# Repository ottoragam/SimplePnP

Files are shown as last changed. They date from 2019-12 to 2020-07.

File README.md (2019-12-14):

# SimplePnP
Your personal open-hardware PCB assembly machine

----------------------------------------------------------------------
SimplePnP (c) by Gino Magarotto

SimplePnP is licensed under a
Creative Commons Attribution-ShareAlike 3.0 Unported License.

You should have received a copy of the license along with this
work.  If not, see <http://creativecommons.org/licenses/by-sa/3.0/>.

----------------------------------------------------------------------
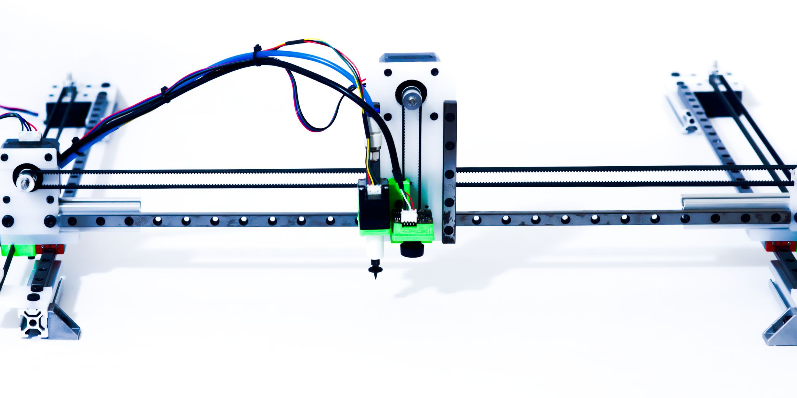
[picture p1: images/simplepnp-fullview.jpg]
drive


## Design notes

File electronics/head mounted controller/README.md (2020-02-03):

Small form factor ATmega328p based GRBL booard. Connects to TMC2209 stepper driver board.

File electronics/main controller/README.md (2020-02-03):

Small form factor ATmega328p based GRBL booard. Connects to TMC2209 stepper driver board. For controlling the pick and place table motors. Needs two USB-UART converter cables like ones based around CH340 and CP2102 chips.

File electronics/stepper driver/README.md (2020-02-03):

Carrier board for three TMC2209 stepper drivers. Standard and serial pins broken out. Fixed current limit.

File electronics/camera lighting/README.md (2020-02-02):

LED carrier board for pick and place camera illumination. 5V PWM input.

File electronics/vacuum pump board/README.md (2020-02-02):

Mosfet switch board for 12VDC vacuum pump. Solder the motor terminals directly to the PCB.

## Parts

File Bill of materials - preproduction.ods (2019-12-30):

Bill of materials for SimplePnP
Part | Qty | Notes
bridge-carriageplate | 2 | custom design for SimplePnP
gt2-idlerbracket | 3 | custom design for SimplePnP
nema17-bracket | 3 | custom design for SimplePnP
vacuum-head | 1 | custom design for SimplePnP
100mm 2020 extrusion | 6 | generic
M5x8 bolt | 20 | socket head or button head
M5 T-slot nut | 20 | generic
M3x6 bolt | 55 | socket head
M3x6 flat head bolt | 20 | socket head
M3x12 bolt | 14 | socket head
M3 T-slot nut | 12 | generic
M3 9mm brass standoff | 6 | 10mm works but may need a flat washer to remove pulley play
axisbelt-clamp | 3 | custom design for SimplePnP
headbelt-clamp | 2 | custom design for SimplePnP
headcamera-bracket | 1 | custom design for SimplePnP
nema8-bracket | 2 | custom design for SimplePnP
Bottomcamera-mount | 1 | custom design for SimplePnP
nema8 motor 8HY0001-7SK | 2
nema17 motor 17HS4023 | 4
drag chain 10x10 or 10x15 | 2
angle bracket for 2020 extrusion | 4 | generic
gt2 driven pulley 16t 5mm bore | 4 | good ones provide better precision
gt2 idler pulley 3mm ID bearing | 4 | good ones provide better precision
gt2 6mm belt 3 or 5 meters | 1 | good ones provide better precision
stepper driver TMC2209 | 6 | custom design for SimplePnP or external drivers
GRBL controller | 2 | custom design for SimplePnP or Arduino with GRBL
stepper motor cables | 6 | user’s preference
air tubing 4x2.5 OdxID 5 meter | 1 | cut in half
MGN9 350mm rail | 3 | generic
MGN9 100mm rail | 2 | generic
MGN9 carriage | 5 | MGN9C carriage by default, MGN9H can be used with alternative hole pattern design (soon)
camera module OV9712 | 2 | 2.1 and 2.8mm focal length
power supply 12V 80W | 1
vacuum pump -40 kPa 10 lpm | 1 | can use two instead of valves for dual heads
M6 rotary fitting for 4mm OD tubing | 2 | generic
reduction fitting | 1 | depends on pump inlet
rotary fitting coupler 5x15mm IDxLength | 2 | M6 threads on one side for rotary fitting (see model in the repo for more info)
nozzle coupler | 2 | betztechnik.ca
Dowel pin 3x16mm OdxLenght | 3 | idler pulley axis, if possible H10 or better tolerance
vacuum nozzles Juki 5xx | 3 | default 503, 504 and 505, extra 506, 507 and 508
M2x6 bolt |  | socket head
Tools
M3-0.5 tap |  | for bridge and head plates

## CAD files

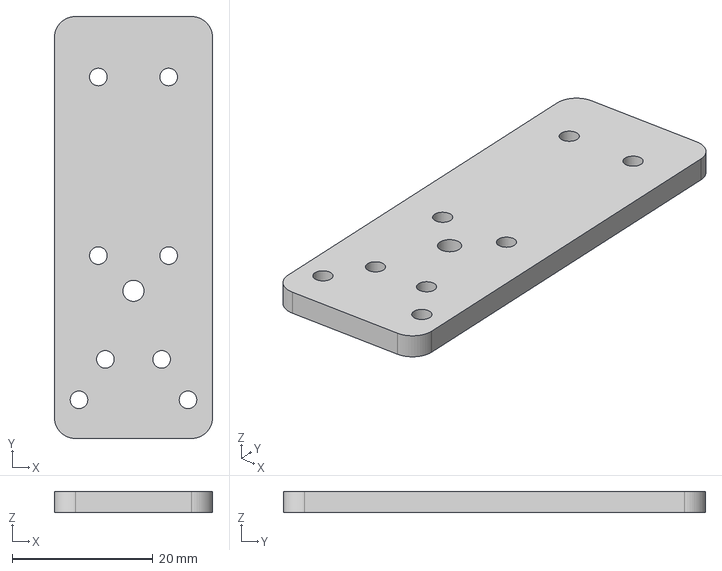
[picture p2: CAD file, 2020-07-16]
mechanical/lswitch-bracket.step
22.5 x 60.0 x 3.00 mm

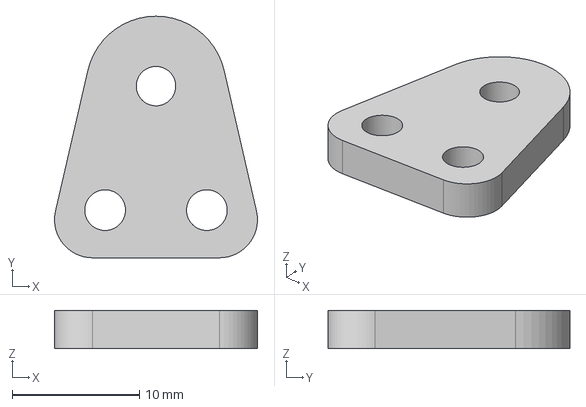
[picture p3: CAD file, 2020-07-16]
mechanical/pulley-bracket.step
16.0 x 19.0 x 3.00 mm

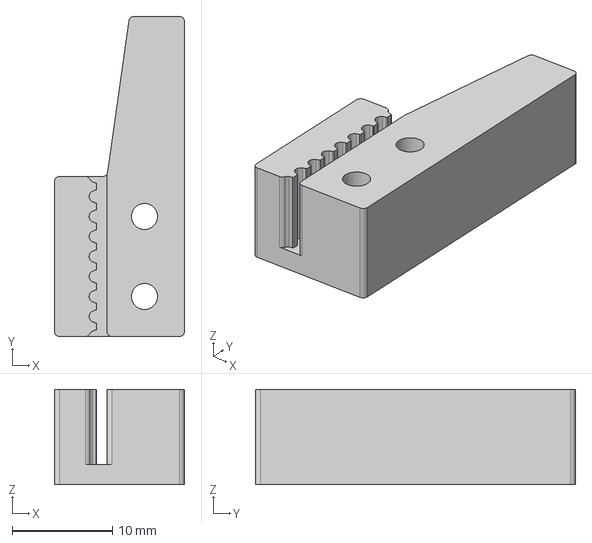
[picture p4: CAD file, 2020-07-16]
mechanical/belt-clamp-right.step
13.0 x 32.0 x 9.50 mm

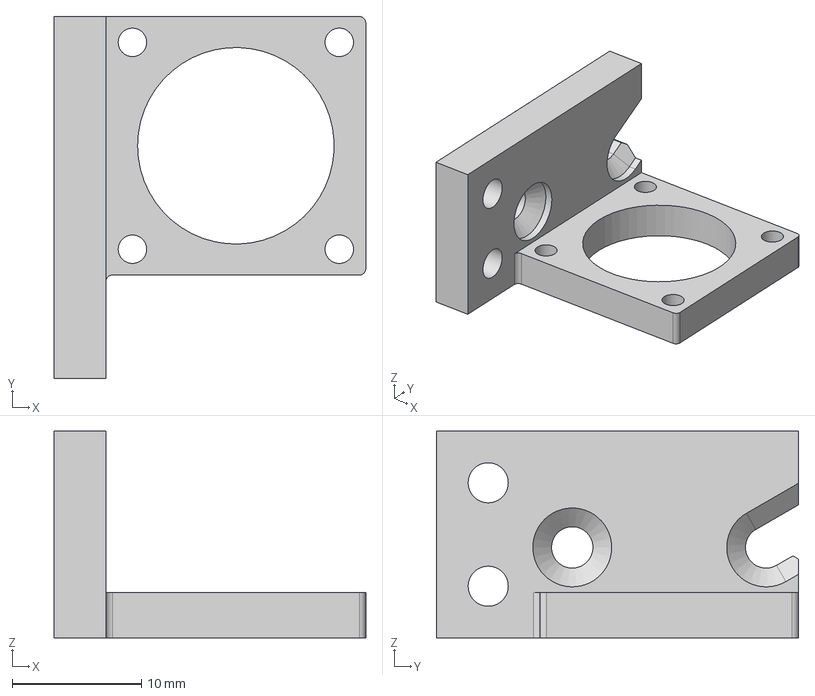
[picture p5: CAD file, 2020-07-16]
mechanical/nema8-mount-right.step
24.1 x 28.0 x 16.0 mm

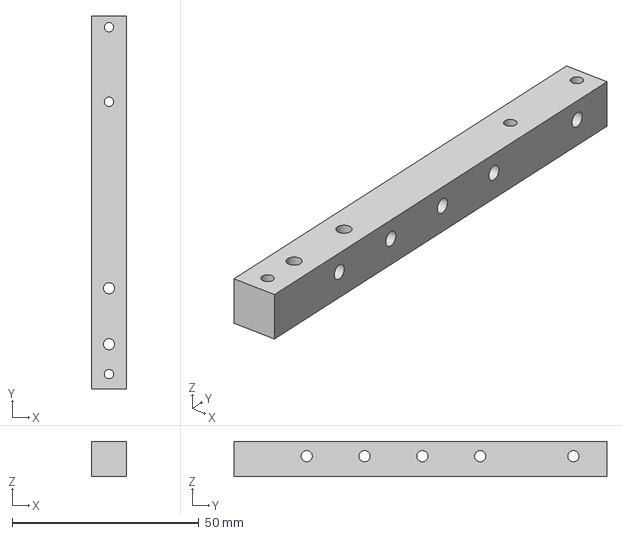
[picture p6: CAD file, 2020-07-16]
mechanical/rail-mount.step
9.50 x 100.0 x 9.50 mm

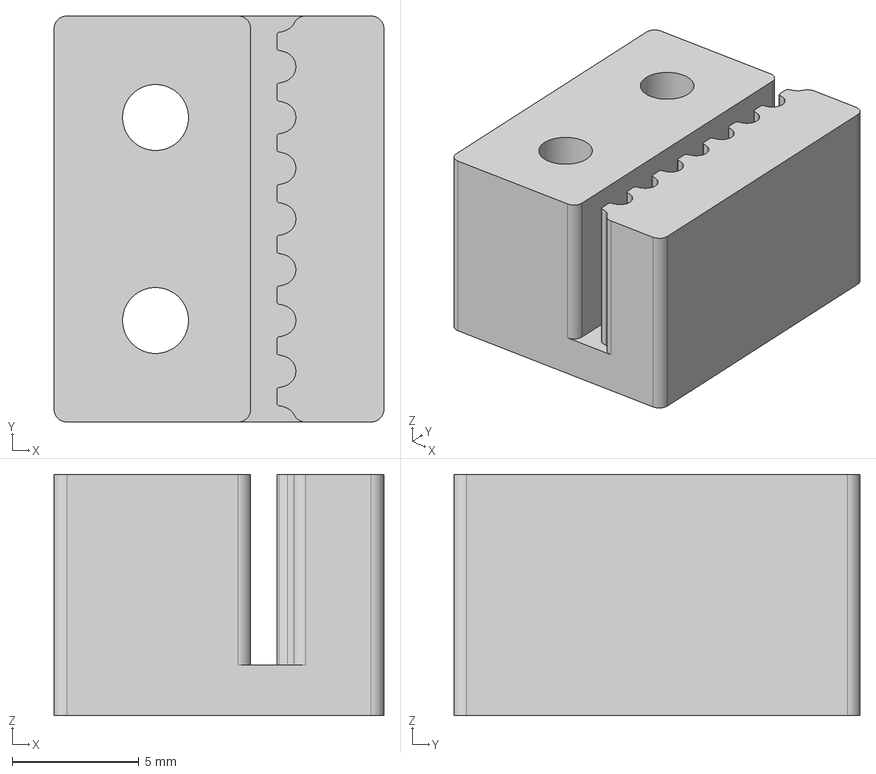
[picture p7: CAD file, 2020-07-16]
mechanical/belt-clamp-left.step
13.0 x 16.0 x 9.50 mm

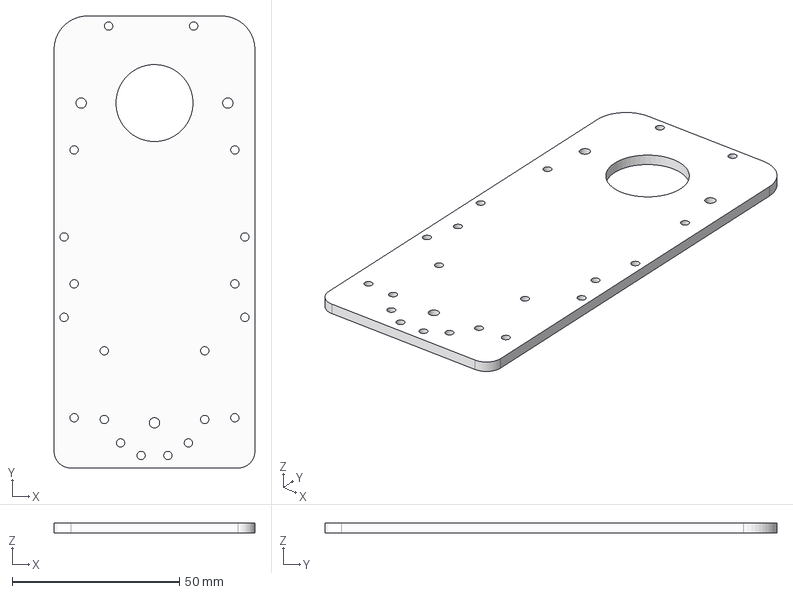
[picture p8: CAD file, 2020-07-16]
mechanical/head-plate.step
60.0 x 135.0 x 3.00 mm

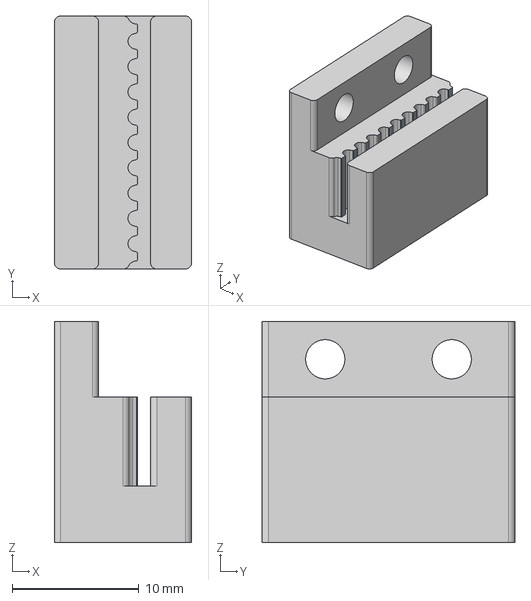
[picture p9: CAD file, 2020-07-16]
mechanical/belt-clamp-x.step
10.8 x 20.0 x 17.5 mm

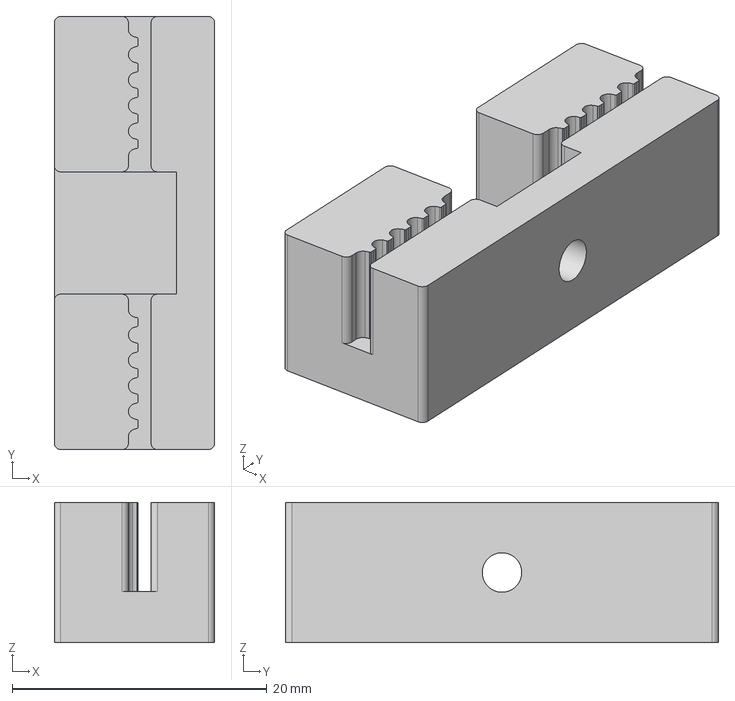
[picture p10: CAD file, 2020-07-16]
mechanical/belt-clamp-y.step
12.6 x 34.0 x 11.0 mm

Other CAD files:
mechanical/nema8-mount-left.step

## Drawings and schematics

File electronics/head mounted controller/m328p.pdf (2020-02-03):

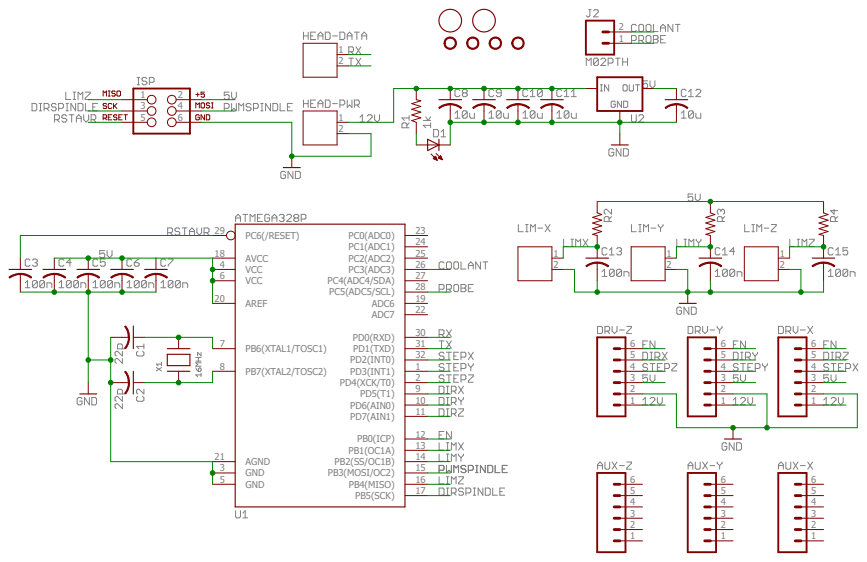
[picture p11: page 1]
PB5(SCK); 17 PB7(XTAL2/TOSC2) 8; PB6(XTAL1/TOSC1) 7; GND 3; GND 5; VCC 4; VCC 6; AGND 21; AREF 20; AVCC 18; PB4(MISO); 16 PB3(MOSI/OC2); 13 PB0(ICP); PD7(AIN1); 11 PD6(AIN0); 9 PD4(XCK/T0); 2 PD3(INT1); 1 PD2(INT0); 32 PD1(TXD); 31 PD0(RXD); ADC7; 22 ADC6; 19 PC5(ADC5/SCL); 28 PC4(ADC4/SDA); 27 PC3(ADC3); 26 PC2(ADC2); 25 PC1(ADC1); 24 PC0(ADC0); 23 PC6(/RESET) 29

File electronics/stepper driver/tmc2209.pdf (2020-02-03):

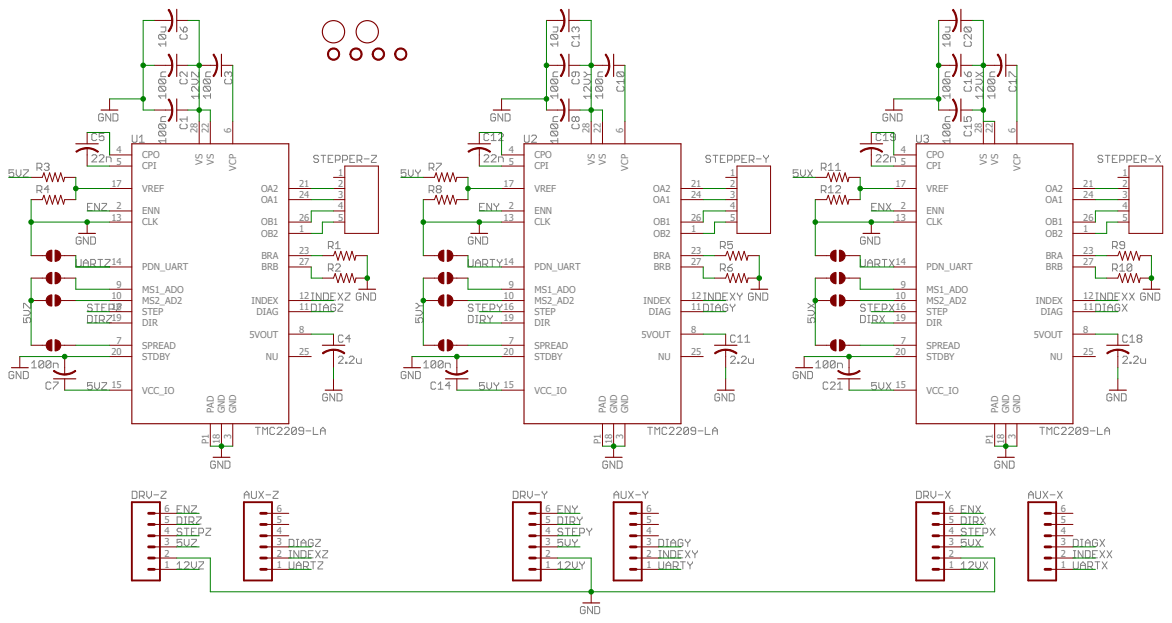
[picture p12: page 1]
1 ENN 2; GND 3 CPO 4; CPI 5; VCP 6 SPREAD 7; 5VOUT; MS1_ADO 9 MS2_AD2 10; DIAG; 11 INDEX; CLK 13; PDN_UART 14; VCC_IO 15; STEP 16; VREF 17; GND 18 DIR 19; STDBY 20; BRA; 26 BRB; 27 VS 28 PAD P1; 27 VS 28 PAD P1 123456

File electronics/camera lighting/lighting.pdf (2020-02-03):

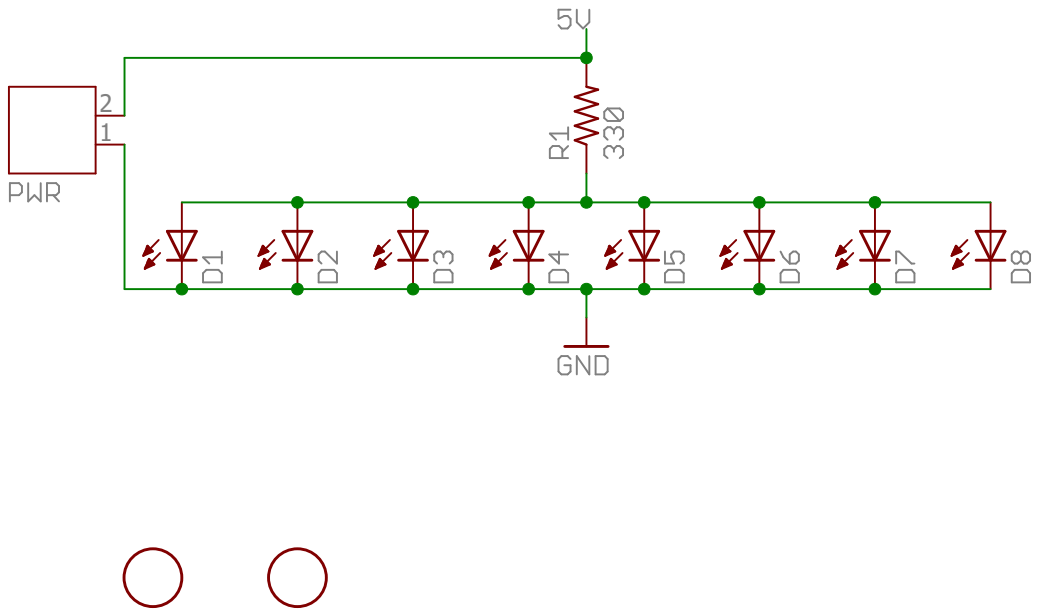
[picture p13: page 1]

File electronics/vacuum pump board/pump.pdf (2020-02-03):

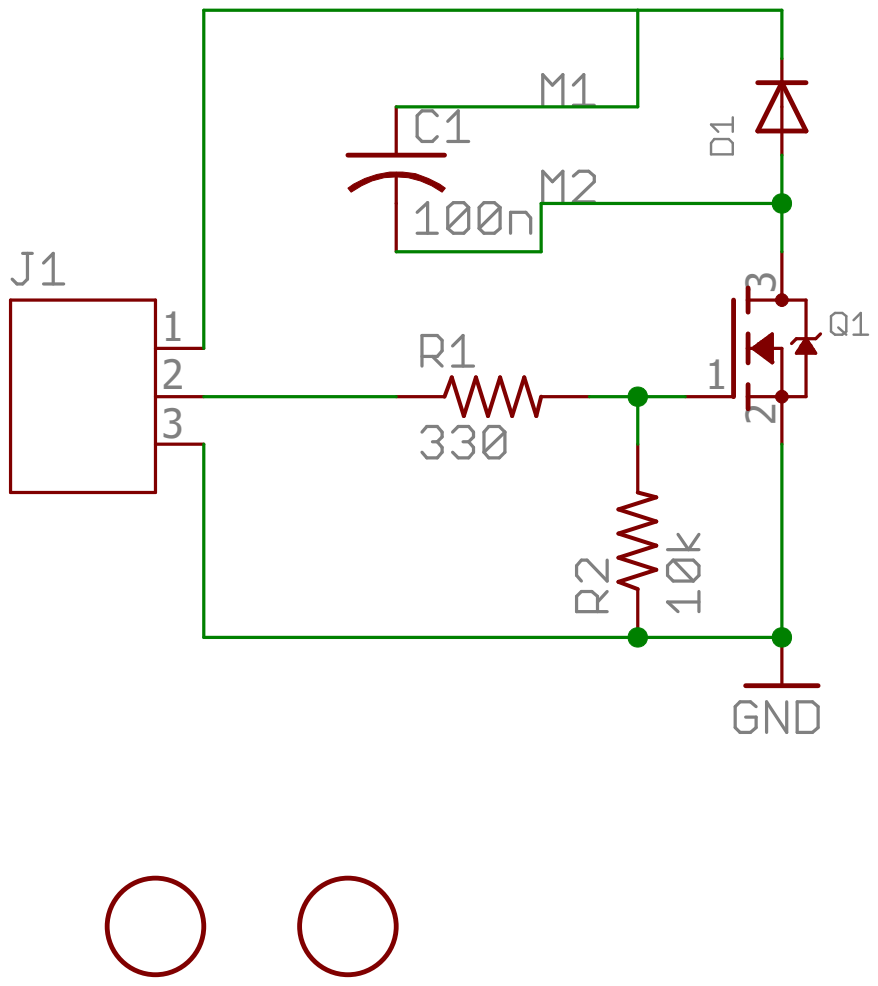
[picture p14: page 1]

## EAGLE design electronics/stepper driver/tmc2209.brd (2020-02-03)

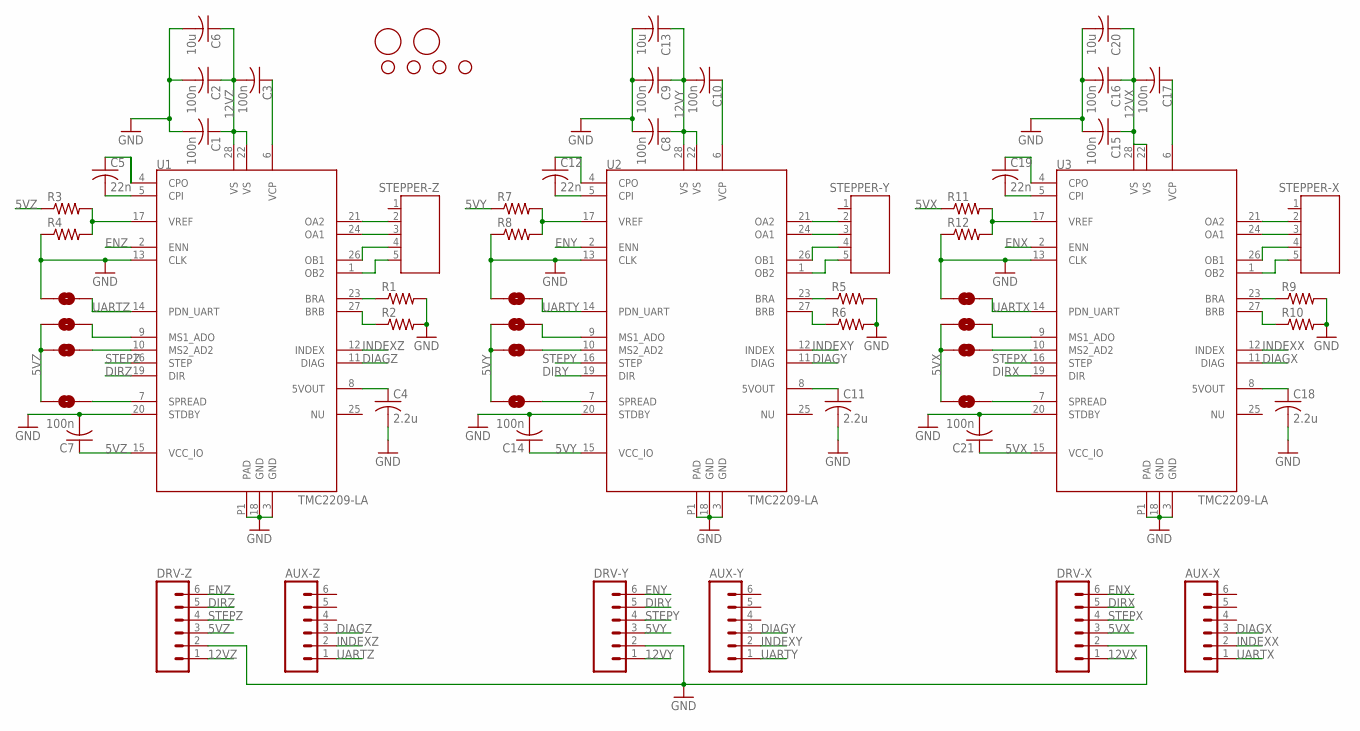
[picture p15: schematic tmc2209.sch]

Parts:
AUX-X: M06LOCK; 1X06_LOCK
AUX-Y: M06LOCK; 1X06_LOCK
AUX-Z: M06LOCK; 1X06_LOCK
C1, C2, C3, C7, C8, C9, C10, C14, C15, C16, C17, C21: 100n; C0603
C4, C11, C18: 2.2u; C1206
C5, C12, C19: 22n; C0603
C6, C13, C20: 10u; C1206
DRV-X: M06LOCK; 1X06_LOCK
DRV-Y: M06LOCK; 1X06_LOCK
DRV-Z: M06LOCK; 1X06_LOCK
PDX: SOLDERJUMPERNO; SJ_2S-NO
PDY: SOLDERJUMPERNO; SJ_2S-NO
PDZ: SOLDERJUMPERNO; SJ_2S-NO
R1, R2, R5, R6, R9, R10: R-US_R0805; R0805
R3, R4, R7, R8, R11, R12: R-US_R0603; R0603
SJ2, SJ3, SJ5, SJ6, SJ8, SJ9, SJ10, SJ11, SJ12: SOLDERJUMPERNO; SJ_2S-NO
STANDOFF1, STANDOFF2, STANDOFF3, STANDOFF4: STAND-OFFTIGHT; STAND-OFF-TIGHT
STEPPER-X: JST-PH5
STEPPER-Y: JST-PH5
STEPPER-Z: JST-PH5
U1, U2, U3: TMC2209-LA; QFN28-5X5-XLEP
U$1, U$2: FIDUCIAL; FIDUCIAL_1MM

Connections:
5VX: C21.1, DRV-X.3, R11.1, SJ8.1, SJ9.1, SJ12.1, U3.15 (VCC_IO)
5VY: C14.1, DRV-Y.3, R7.1, SJ5.1, SJ6.1, SJ11.1, U2.15 (VCC_IO)
5VZ: C7.1, DRV-Z.3, R3.1, SJ2.1, SJ3.1, SJ10.1, U1.15 (VCC_IO)
12VX: C15.1, C16.1, C17.2, C20.1, DRV-X.1, U3.22 (VS), U3.28 (VS)
12VY: C8.1, C9.1, C10.2, C13.1, DRV-Y.1, U2.22 (VS), U2.28 (VS)
12VZ: C1.1, C2.1, C3.2, C6.1, DRV-Z.1, U1.22 (VS), U1.28 (VS)
DIAGX: AUX-X.3, U3.11 (DIAG)
DIAGY: AUX-Y.3, U2.11 (DIAG)
DIAGZ: AUX-Z.3, U1.11 (DIAG)
DIRX: DRV-X.5, U3.19 (DIR)
DIRY: DRV-Y.5, U2.19 (DIR)
DIRZ: DRV-Z.5, U1.19 (DIR)
ENX: DRV-X.6, U3.2 (ENN)
ENY: DRV-Y.6, U2.2 (ENN)
ENZ: DRV-Z.6, U1.2 (ENN)
GND: C1.2, C2.2, C4.2, C6.2, C7.2, C8.2, C9.2, C11.2, C13.2, C14.2, C15.2, C16.2, C18.2, C20.2, C21.2, DRV-X.2, DRV-Y.2, DRV-Z.2, PDX.1, PDY.1, PDZ.1, R1.2, R2.2, R4.1, R5.2, R6.2, R8.1, R9.2, R10.2, R12.1, U1.3 (GND), U1.13 (CLK), U1.18 (GND), U1.20 (STDBY), U1.P1 (PAD), U2.3 (GND), U2.13 (CLK), U2.18 (GND), U2.20 (STDBY), U2.P1 (PAD), U3.3 (GND), U3.13 (CLK), U3.18 (GND), U3.20 (STDBY), U3.P1 (PAD)
INDEXX: AUX-X.2, U3.12 (INDEX)
INDEXY: AUX-Y.2, U2.12 (INDEX)
INDEXZ: AUX-Z.2, U1.12 (INDEX)
unnamed: STEPPER-Z.5, U1.1 (OB2)
unnamed: STEPPER-Z.4, U1.26 (OB1)
unnamed: STEPPER-Z.3, U1.24 (OA1)
unnamed: STEPPER-Z.2, U1.21 (OA2)
unnamed: STEPPER-Y.5, U2.1 (OB2)
unnamed: STEPPER-Y.4, U2.26 (OB1)
unnamed: STEPPER-Y.3, U2.24 (OA1)
unnamed: STEPPER-Y.2, U2.21 (OA2)
unnamed: STEPPER-X.2, U3.21 (OA2)
unnamed: STEPPER-X.3, U3.24 (OA1)
unnamed: STEPPER-X.4, U3.26 (OB1)
unnamed: STEPPER-X.5, U3.1 (OB2)
unnamed: R5.1, U2.23 (BRA)
unnamed: C11.1, U2.8 (5VOUT)
unnamed: SJ2.2, U1.9 (MS1_ADO)
unnamed: SJ3.2, U1.10 (MS2_AD2)
unnamed: SJ6.2, U2.10 (MS2_AD2)
unnamed: R6.1, U2.27 (BRB)
unnamed: C18.1, U3.8 (5VOUT)
unnamed: C17.1, U3.6 (VCP)
unnamed: C12.2, U2.5 (CPI)
unnamed: C12.1, U2.4 (CPO)
unnamed: C19.2, U3.5 (CPI)
unnamed: SJ5.2, U2.9 (MS1_ADO)
unnamed: C19.1, U3.4 (CPO)
unnamed: SJ12.2, U3.7 (SPREAD)
unnamed: SJ11.2, U2.7 (SPREAD)
unnamed: SJ9.2, U3.10 (MS2_AD2)
unnamed: SJ8.2, U3.9 (MS1_ADO)
unnamed: R11.2, R12.2, U3.17 (VREF)
unnamed: R7.2, R8.2, U2.17 (VREF)
unnamed: C10.1, U2.6 (VCP)
unnamed: SJ10.2, U1.7 (SPREAD)
unnamed: R9.1, U3.23 (BRA)
unnamed: R10.1, U3.27 (BRB)
unnamed: R1.1, U1.23 (BRA)
unnamed: R2.1, U1.27 (BRB)
unnamed: R3.2, R4.2, U1.17 (VREF)
unnamed: C4.1, U1.8 (5VOUT)
unnamed: C5.2, U1.5 (CPI)
unnamed: C5.1, U1.4 (CPO)
unnamed: C3.1, U1.6 (VCP)
STEPX: DRV-X.4, U3.16 (STEP)
STEPY: DRV-Y.4, U2.16 (STEP)
STEPZ: DRV-Z.4, U1.16 (STEP)
UARTX: AUX-X.1, PDX.2, U3.14 (PDN_UART)
UARTY: AUX-Y.1, PDY.2, U2.14 (PDN_UART)
UARTZ: AUX-Z.1, PDZ.2, U1.14 (PDN_UART)

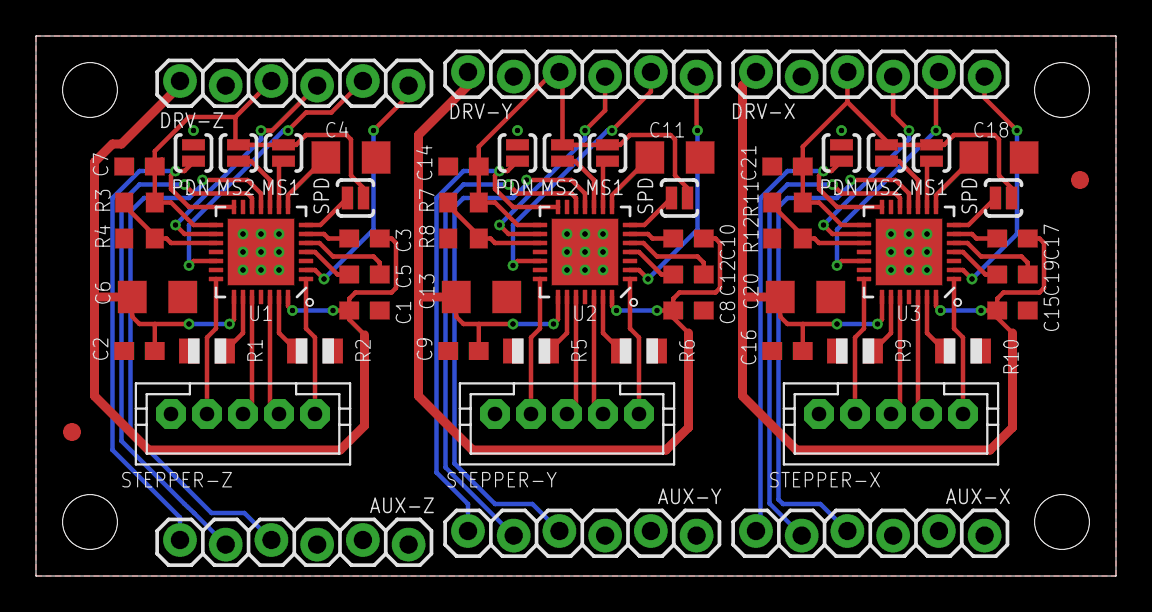
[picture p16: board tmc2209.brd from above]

Board: 2 copper layers, 60.0 x 30.0 mm, 63 parts (0 on the bottom side), 67 nets.

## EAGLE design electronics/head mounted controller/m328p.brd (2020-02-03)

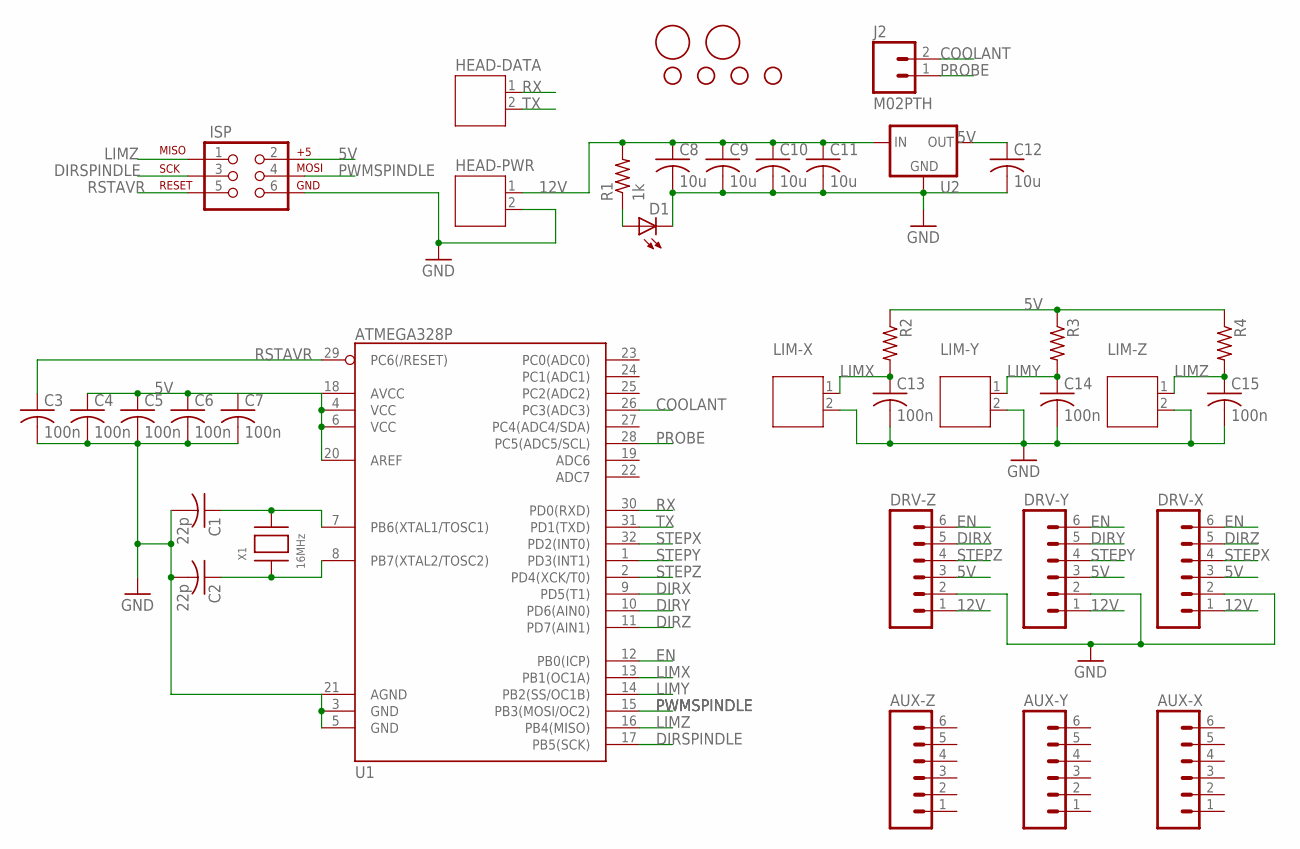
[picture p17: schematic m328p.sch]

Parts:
AUX-X: M06LOCK; 1X06_LOCK
AUX-Y: M06LOCK; 1X06_LOCK
AUX-Z: M06LOCK; 1X06_LOCK
C1, C2: 22p; C0603
C3, C4, C5, C6, C7, C13, C14, C15: 100n; C0603
C8, C9, C10, C11, C12: 10u; C1206
D1: LEDCHIPLED_1206; CHIPLED_1206
DRV-X: M06LOCK; 1X06_LOCK
DRV-Y: M06LOCK; 1X06_LOCK
DRV-Z: M06LOCK; 1X06_LOCK
HEAD-DATA: JST-PH2
HEAD-PWR: JST-PH2
ISP: AVR_SPI_PRG_6PTH; 2X3
J2: M02PTH; 1X02
LIM-X: JST-PH2
LIM-Y: JST-PH2
LIM-Z: JST-PH2
R1: 1k; R1206
R2, R3, R4: R-US_R0603; R0603
STANDOFF1, STANDOFF2, STANDOFF3, STANDOFF4: STAND-OFFTIGHT; STAND-OFF-TIGHT
U1: ATMEGA328P; TQFP32-08
U2: V_REG_MIC2920; SOT223
U$1, U$2: FIDUCIAL; FIDUCIAL_1MM
X1: 16MHz; XTAL3215

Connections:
5V: C4.1, C5.1, C6.1, C7.1, C12.1, DRV-X.3, DRV-Y.3, DRV-Z.3, ISP.2, R2.1, R3.1, R4.1, U1.4 (VCC), U1.6 (VCC), U1.18 (AVCC), U1.20 (AREF), U2.3 (OUT)
12V: C8.1, C9.1, C10.1, C11.1, DRV-X.1, DRV-Y.1, DRV-Z.1, HEAD-PWR.1, R1.2, U2.1 (IN)
COOLANT: J2.2, U1.26 (PC3(ADC3))
DIRSPINDLE: ISP.3, U1.17 (PB5(SCK))
DIRX: DRV-Z.5, U1.9 (PD5(T1))
DIRY: DRV-Y.5, U1.10 (PD6(AIN0))
DIRZ: DRV-X.5, U1.11 (PD7(AIN1))
EN: DRV-X.6, DRV-Y.6, DRV-Z.6, U1.12 (PB0(ICP))
GND: C1.2, C2.2, C3.2, C4.2, C5.2, C6.2, C7.2, C8.2, C9.2, C10.2, C11.2, C12.2, C13.2, C14.2, C15.2, D1.C, DRV-X.2, DRV-Y.2, DRV-Z.2, HEAD-PWR.2, ISP.6, LIM-X.2, LIM-Y.2, LIM-Z.2, U1.3 (GND), U1.5 (GND), U1.21 (AGND), U2.2 (GND), U2.4 (GND)
LIMX: C13.1, LIM-X.1, R2.2, U1.13 (PB1(OC1A))
LIMY: C14.1, LIM-Y.1, R3.2, U1.14 (PB2(SS/OC1B))
LIMZ: C15.1, ISP.1, LIM-Z.1, R4.2, U1.16 (PB4(MISO))
unnamed: C1.1, U1.7 (PB6(XTAL1/TOSC1)), X1.P$2
unnamed: C2.1, U1.8 (PB7(XTAL2/TOSC2)), X1.P$1
unnamed: D1.A, R1.1
PROBE: J2.1, U1.28 (PC5(ADC5/SCL))
PWMSPINDLE: ISP.4, U1.15 (PB3(MOSI/OC2))
RSTAVR: C3.1, ISP.5, U1.29 (PC6(/RESET))
RX: HEAD-DATA.1, U1.30 (PD0(RXD))
STEPX: DRV-X.4, U1.32 (PD2(INT0))
STEPY: DRV-Y.4, U1.1 (PD3(INT1))
STEPZ: DRV-Z.4, U1.2 (PD4(XCK/T0))
TX: HEAD-DATA.2, U1.31 (PD1(TXD))

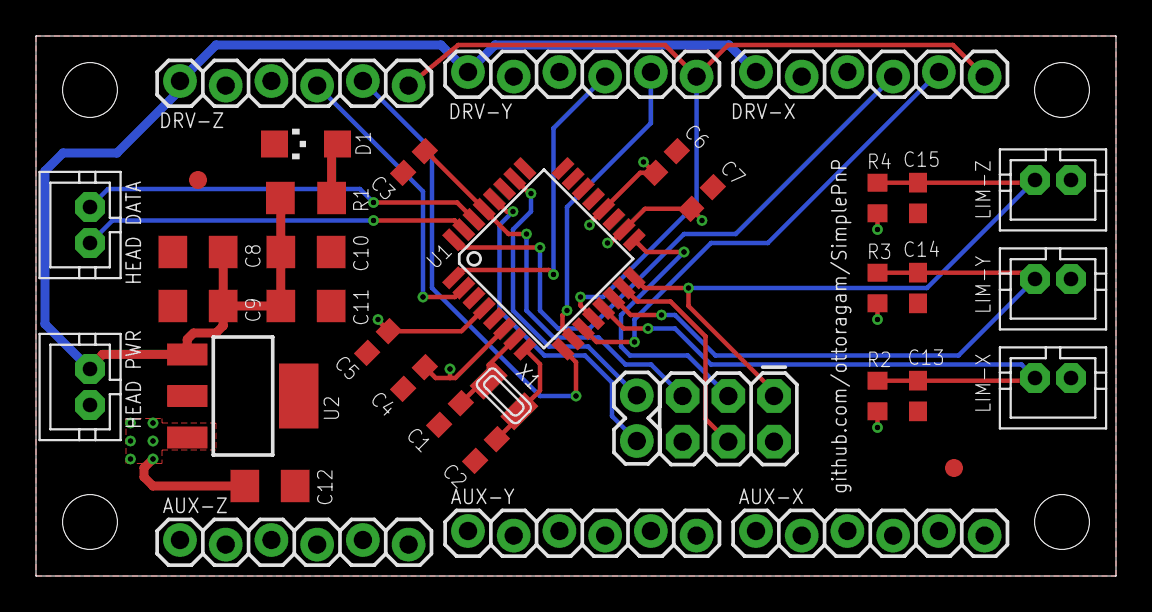
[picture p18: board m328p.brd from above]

Board: 2 copper layers, 60.0 x 30.0 mm, 42 parts (0 on the bottom side), 23 nets.

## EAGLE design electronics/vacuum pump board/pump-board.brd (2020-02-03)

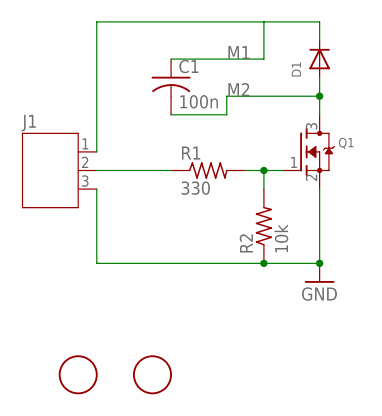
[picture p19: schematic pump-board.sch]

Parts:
C1: 100n; C1206
D1: DIODESOD-123; SOD-123
J1: JST-PH3
Q1: MOSFET-NREFLOW; SOT23
R1: 330; R1206
R2: 10k; R1206
U$1, U$2: FIDUCIAL; FIDUCIAL_1MM

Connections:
GATE: Q1.1 (G), R1.2, R2.2
GND: J1.3, Q1.2 (S), R2.1
M1: C1.1, D1.C, J1.1
M2: C1.2, D1.A, Q1.3 (D)
unnamed: J1.2, R1.1

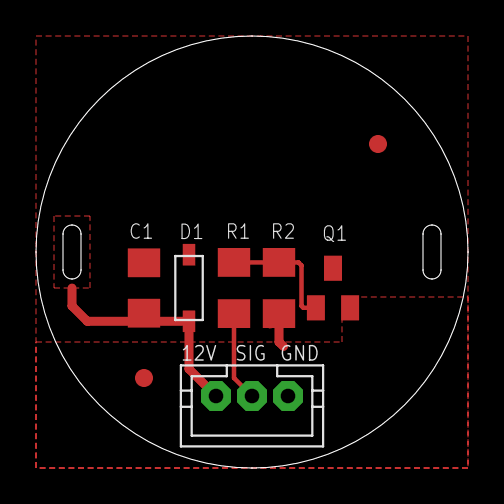
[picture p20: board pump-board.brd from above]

Board: 2 copper layers, 24.0 x 24.0 mm, 8 parts (0 on the bottom side), 5 nets.

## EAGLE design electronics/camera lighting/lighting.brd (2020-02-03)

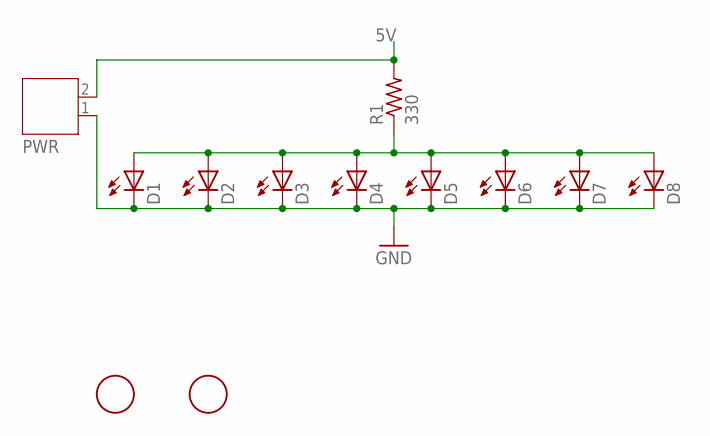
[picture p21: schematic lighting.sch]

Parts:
D1, D2, D3, D4, D5, D6, D7, D8: LEDCHIPLED_1206; CHIPLED_1206
PWR: JST-PH2
R1: 330; R1206
U$1, U$2: FIDUCIAL; FIDUCIAL_1MM

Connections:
5V: PWR.2, R1.2
COMMON: D1.A, D2.A, D3.A, D4.A, D5.A, D6.A, D7.A, D8.A, R1.1
GND: D1.C, D2.C, D3.C, D4.C, D5.C, D6.C, D7.C, D8.C, PWR.1

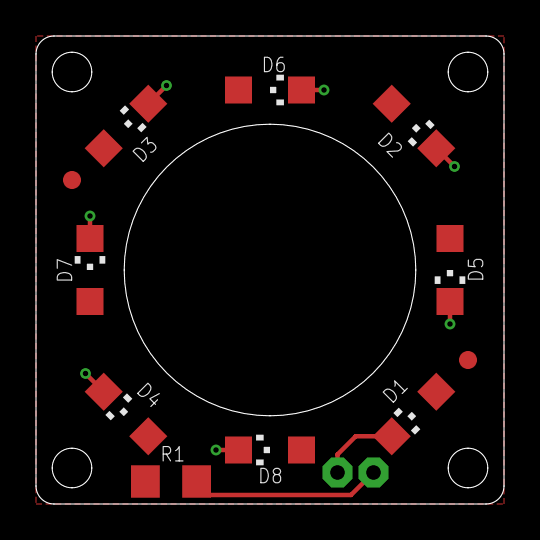
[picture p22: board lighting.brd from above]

Board: 2 copper layers, 26.0 x 26.0 mm, 12 parts (1 on the bottom side), 3 nets.

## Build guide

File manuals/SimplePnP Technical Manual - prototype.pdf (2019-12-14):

SimplePnP

Technical Manual

# Contents

Revision 2019-09-03 | 1

Technical Manual

# Overview and Features

SimplePnP is a Cartesian pick and place machine. It can be divided in two parts: the head and the table.

The head is the part used to grab electronic components meant to be installed on a PCB. It uses a hollow shaft stepper motor to rotate the parts and allow a DC vacuum pump to hold them with different sized nozzles and a camera to help locating features and components.

The table is meant to position the head in the correct spot to hold and release each component. It is a gantry style system built from aluminum extrusion and uses linear rails, stepper motors and timing belts to perform motion.

A computer running OpenPnP is used as the brains of the machine, which sends the appropriate commands to a pair of GRBL motion controllers that handle the operations needed to perform the PCB assembly job.

Its specs are as follows:

X travel | 300 mm
Y travel | 300 mm
Z travel | 23 mm
Footprint | 650×500×200 mm
CPH | 750 | With vision assist
Component size | Up to 0402 (1005 metric)
Nozzle type | Samsung CP45
Vision | Top vision | Optional bottom vision
Number of Heads | 1 (base model) | Optional dual head
Power consumption | 60 W | With a 12 V power supply
Weight | 4 kg | Bench mountable

Technical Manual

# GRBL

This machine uses a pair of Arduino based GRBL controllers with V1.1 firmware for both the Cartesian table and vacuum head. Only the controller parameters will be presented in this manual. Instructions on how to configure GRBL are available on the web.

## Parameters

Table | Head | Table | Head
$0=10 | $0=10 | $26=250 | $26=250
$1=50 | $1=255 | $27=1.000 | $27=1.000
$2=0 | $2=0 | $30=1000 | $30=1000
$3=0 | $3=1 | $31=0 | $31=0
$4=0 | $4=0 | $32=0 | $32=0
$5=1 | $5=1 | $100=50.000 | $100=50.000
$6=0 | $6=0 | $101=50.000 | $101=50.000
$10=1 | $10=1 | $102=50.000 | $102=4.444
$11=0.010 | $11=0.010 | $110=20000.000 | $110=18000.000
$12=0.002 | $12=0.002 | $111=20000.000 | $111=18000.000
$13=0 | $13=0 | $112=20000.000 | $112=18000.000
$20=1 | $20=0 | $120=1000.000 | $120=1000.000
$21=0 | $21=0 | $121=1000.000 | $121=1000.000
$22=1 | $22=1 | $122=1000.000 | $122=1000.000
$23=7 | $23=0 | $130=310.000 | $130=23.000
$24=25.000 | $24=25.000 | $131=310.000 | $131=23.000
$25=1000.000 | $25=1000.000 | $132=310.000 | $132=360.000

Technical Manual

# OpenPnP

OpenPnP is a Java based open source software program that can be used with this machine in order to program and run PCB assembly jobs. This section of the manual will cover the configuration of machine drivers, head and feeders. In depth
information | about | configuring | OpenPnP | can | be | found | at
https://github.com/openpnp/openpnp/wiki

# Machine Drivers

A machine driver contains all the info pertaining the communication between a motion controller (GRBL in this case) and a computer running OpenPnP. SimplePnP uses two separate motion controllers, one for the table and another one for the head, so we need to set up the table driver and the head sub driver.

## Table Driver Setup

| Setting | | | Message
COMMAND_CONFIRM_REGEX | OK
CONNECT_COMMAND | $X
| | G90
HOME_COMMAND | $H
G92 X0 Y0 Z0
MOVE_TO_COMMAND | G1 {Y:X%.4f} {Y:Y%.4f} {X:Z%.4f} F{FeedRate:%.0f}
| | G4 P0
PICK_COMMAND | | M8
PLACE_COMMAND | M9

Technical Manual

## Head Sub Driver

Setting | Message
COMMAND_CONFIRM_REGEX | OK
CONNECT_COMMAND | $X G90
HOME_COMMAND | G92 X0 Y0 Z0
MOVE_TO_COMMAND | G1 {Z:X%.4f} {Rotation:Z%.4f} F{FeedRate:%.0f} G4 P0

Technical Manual

The machine.xml sub driver section should look like this:

<sub-drivers class="java.util.ArrayList">
<gcode-driver communications="serial" connection-keep-alive="false" units="Millimeters" max-feed-rate="18000" backlash-offset-x="-1.0" backlash-offset-y="-1.0" non-squareness-factor="0.0" backlash-feed-rate-factor="0.1" timeout-milliseconds="5000" connect-wait-time-milliseconds="3000" visual-homing-enabled="true" name="GcodeDriver">
<serial line-ending-type="LF" port-name="COM5" baud="115200" flow-control="Off" data-bits="Eight" stop-bits="One" parity="None" set-dtr="false" set-rts="false" name="SerialPortCommunications"/>
<tcp line-ending-type="LF" ip-address="127.0.0.1" port="23" name="TcpCommunications"/> <homing-fiducial-location units="Millimeters" x="0.0" y="0.0" z="0.0" rotation="0.0"/>
<command type="COMMAND_CONFIRM_REGEX"> <text><![CDATA[ok]]></text>
</command>
<command type="MOVE_TO_COMMAND">
<text><![CDATA[G1 {Z:X%.4f} {Rotation:Z%.4f} F{FeedRate:%.0f}]]></text> <text><![CDATA[G4 P0]]></text>
</command>
<command type="CONNECT_COMMAND"> <text><![CDATA[$X]]></text> <text><![CDATA[G90]]></text> </command>
<command type="HOME_COMMAND"> <text><![CDATA[G92 X0 Y0 Z0]]></text> </command>
<sub-drivers class="java.util.ArrayList"/>
<axes class="java.util.ArrayList">
<axis name="z" type="Z" home-coordinate="0.0"> <head-mountable-ids class="java.util.HashSet"> <string>*</string>
</head-mountable-ids>
</axis>
<axis name="rotation" type="Rotation" home-coordinate="0.0"> <head-mountable-ids class="java.util.HashSet"> <string>*</string>
</head-mountable-ids>
</axis>
</axes>
</gcode-driver>
</sub-drivers>

Technical Manual

# Head

The head machine component has the information regarding the nozzle carriage and bottom looking camera parameters and capabilities. OpenPnP allows the user to set the preferred head parking location and it is recommended to set the soft travel limits to:

| X | Y
Minimum | 0 | 0
Maximum | 300 | 300

## Nozzle

To set up a nozzle for the SimplePnP machine, the user needs to do the following:

- Set nozzle X offset to -30
- Activate “Limit Rotation to 180º”
- Set pick and place dwell times to 350 ms
- Create default nozzle tip and mark it as compatible with the nozzle

## Camera

To set up a nozzle for the SimplePnP machine, the user needs to do the following:

- Set top camera as down looking
- Configure units per pixel depending on Z distance from surface
- Calibrate test using built in routine

Technical Manual

## Top Camera Characteristics

- 2.8 mm focal length
- Manual focus
- M12 threaded lens
- USB 2.0 interface
- 1280x720

## Pump specs

- 12 V 10W brushed DC motor
- 10 liters per minute
- 55 kPa max vacuum pressure

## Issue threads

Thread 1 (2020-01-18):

PCB design work

ottoragam, 2020-01-18:
I'm creating this issue to keep track of the progress on the various circuit board designs needed for SimplePnP.

Remaining work:

- Main controller board (very similar to the head mounted controller board)
- Dedicated home switch PCB
- Vacuum pump board

4b11b4, 2020-01-26:
What are the two designs currently in the electronics folder?
(I messaged you via CrowdSupply about helping with a few things for the electronics)

ottoragam, 2020-01-26:
Hi Anton, the designs are for a small form factor GRBL cntroller and three stepper drivers that will be mounted on the machine's head.

4b11b4, 2020-01-26:
Maybe to get started create some directories for each design and
add any documentation (existing off the shelf boards you are using, etc) or
some simple text file of high level functions of what each board is supposed to do?
(just a suggestion)

ottoragam, 2020-01-26:
Good idea, I'll make the changes in a moment.

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

ottoragam, 2020-01-28:
I forgot to list it, but the LED carrier board design for camera illumination is now up.

4b11b4, 2020-02-06:
Any ideas where initial contributions might occur?

ottoragam, 2020-02-06:
Let me see how the designs work. I'm waitong for the PCBs to be shipped from China.

4b11b4, 2020-09-29:
How'd these designs turn out?

ottoragam, 2020-09-30:
Hey, I've not been able yet to start working ith the PCBs. I'll post here again when I get things moving.

nickbetteridge, 2020-11-25:
Do you have any plans to add a solder dispenser?

4b11b4, 2020-11-28:
I am still interested in helping out with a small piece of the electronics --- I have a purely software job as of recently and I miss working with hardware already!

ottoragam, 2020-11-28:
>
>
> Do you have any plans to add a solder dispenser?

I haven't tested something like that in the machines yet. I plan to start working on the add-ons once I get my crowdfunding machines shipped.

ottoragam, 2020-11-28:
>
>
> I am still interested in helping out with a small piece of the electronics --- I have a purely software job as of recently and I miss working with hardware already!

Apologies, I'm not yet at the PCB assembly stage, but I estimate that it shouldn't take me more than a month to start working on those.

ariefadha, 2021-01-22:
is there any pcb design release yet? because i just see 3 stepper connector on this git
meanwhile PnP need at least 4

ottoragam, 2021-01-22:
@ariefadha Im using two stepper driver boards for controlling up to six motors. I'm just separating the table control from the head control in order to reduce the number of conductors needed for the head (just power and serial data)

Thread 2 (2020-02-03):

PDF of schematics

HarjitSi, 2020-02-03:
Please consider checking a PDF version of the schematic for those that don't have the CAD tool installed but want to take a look.

Thanks.

ottoragam, 2020-02-03:
Thanks for reminding me of that. Give just a moment.

ottoragam, 2020-02-03:
Done, Also added gerbers.

Closed 2020-02-06.

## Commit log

2019-12-14 added prototype 2D drawings
    [axisbelt-clamp-preproduction.stl, bridge-carriageplate-preproduction.dxf, gt2idler-bracket-preproduction.dxf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]
2019-12-15 xml configuration file for prototype machine
2019-12-17 partial BOM
    [Bill of materials - partial.ods]
2019-12-18 subject to change
    [Bill of materials - partial.ods, Bill of materials - preproduction.ods]
2019-12-18 added missig item
    [Bill of materials - preproduction.ods]
2019-12-19 camera spacer
    [headcamera-spacer.stl]
2019-12-19 more updates
    [Bill of materials - preproduction.ods]
2019-12-30 add M2 bolts
    [Bill of materials - preproduction.ods]
2019-12-30 added more stuff
    [Bill of materials - preproduction.ods]
2020-01-17 head mounted grbl
    [m328p-preproduction.brd, m328p-preproduction.sch, tmc2209-preproduction.brd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]
2020-01-26 prper directories and description
    [m328p-preproduction.brd, m328p-preproduction.sch, tmc2209-preproduction.brd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]
2020-01-28 camera lighting
    [lighting.brd, lighting.sch]
2020-01-28 back mounted pump PCB. Net tested for fit
    [pump-board.brd, pump-board.sch]
2020-02-02 pre-production PCBs
    [baseboard.brd, baseboard.sch, lighting.brd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]
2020-02-03 updated all PCBs and added PDF schematics
    [baseboard.brd, baseboard.sch, lighting.brd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]
2020-07-16 production design files
    [axisbelt-clamp-preproduction.stl, belt-clamp-left.step, belt-clamp-right.step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]
2020-07-16 added part
    [lswitch-bracket.step]

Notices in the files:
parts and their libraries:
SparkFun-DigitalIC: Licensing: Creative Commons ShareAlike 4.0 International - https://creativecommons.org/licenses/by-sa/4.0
